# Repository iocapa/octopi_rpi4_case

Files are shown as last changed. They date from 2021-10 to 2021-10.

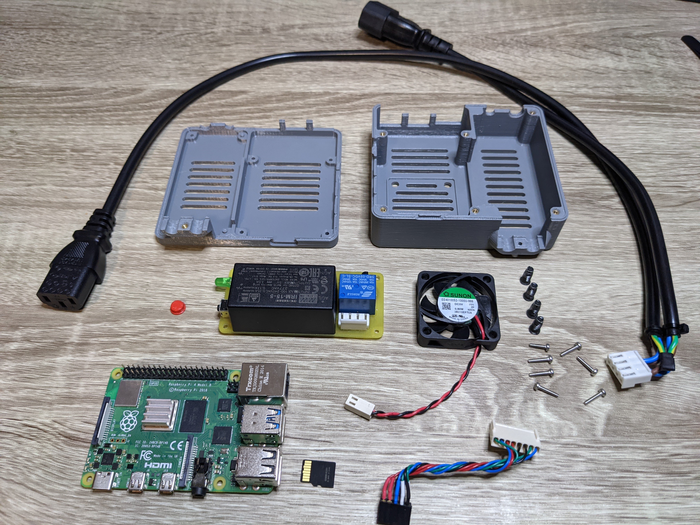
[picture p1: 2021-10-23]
pics/7-parts.jpg

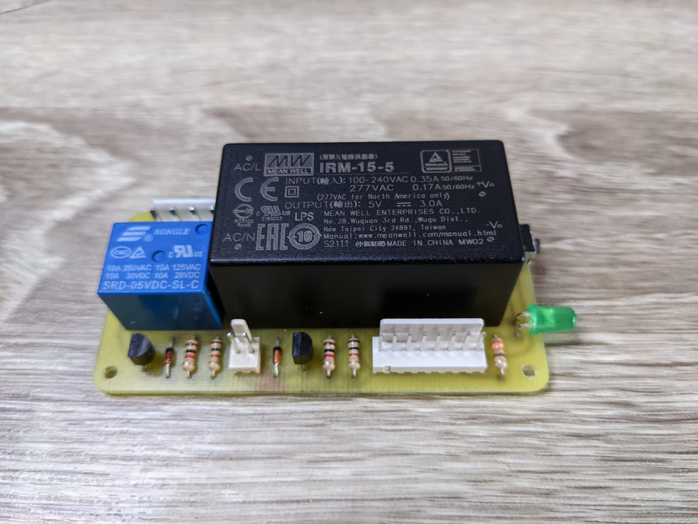
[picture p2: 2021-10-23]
pics/5-assemble.jpg

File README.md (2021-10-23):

Shield: [][cc-by-sa]

This work is licensed under a
[Creative Commons Attribution-ShareAlike 4.0 International License][cc-by-sa].

[][cc-by-sa]

[cc-by-sa]: http://creativecommons.org/licenses/by-sa/4.0/
[cc-by-sa-image]: https://licensebuttons.net/l/by-sa/4.0/88x31.png
[cc-by-sa-shield]: https://img.shields.io/badge/License-CC%20BY--SA%204.0-lightgrey.svg

## Disclaimer ##
Working with mains voltage can be dangerous. Proceed at your own risk.

## Scope ##
* The scope of this project was to create a case for a raspberry pi4 that runs octopi and provides a way to turn off/on the printer (Prusa MK3S+) via the web interface. 
* The project was designed and built during a weekend, therefore it had to be built with parts/tools I had lying around, and it had to be pretty low effort.
* In retrospective, some design decisions were not the "best", but after running this for a week, I'm pretty satisfied with it :).

## Requirements ##
* Shall use a raspberry pi4.
* Shall be compact enough to fit the available space.
* Shall incorporate a relay controllable through the octoprint interface.
* Shall have a status LED.
* Shall have a safe shutdown / power-on button.
* Shall provide active cooling (fan).
* Shall be installable with minimal effort (no mods to the printer).

## Design (Day 1) ##
* ~~Design the [PCB](./pcb/octopi_rpi4_case.pro)~~.
* ~~Design the case [assembly](./assembly/assembly.pdf)~~.

## Build (Day 2) ##
* Print the [top](./pics/11-top.jpg) part of the case and install the brass inserts.
* Cut and [drill](./pics/1-drill.jpg) the blank PCB using the provided [stencil](./pcb/printable/hole_guide.stl).
* [Mask](./pics/2-mask.jpg) the PCB (with a quality permanent marker) using the [template](./pcb/octopi_rpi4_case_bot_mirrored.pdf).
* [Etch](./pics/3-etch.jpg) the PCB.
* [Tin](./pics/4-tin.jpg) the PCB.
* [Populate](./pics/5-assemble.jpg) the PCB using the [template](./pcb/octopi_rpi4_case_silk.pdf) and the [schematic](./pcb/octopi_rpi4_case.pdf).
* [Coat](./pics/6-coat.jpg) the PCB with a thick plastic layer using the provided [mask](./pcb/printable/coating_mask.stl). <span style="color:red">WARNING SKIP THIS AT YOUR OWN RISK</span>, [ECS Plastic 70](https://www.ecsag.com/product/plastic-2/?lang=en) spray works well.
* Print the [bottom](./pics/10-botom-cap.jpg) part of the case and install the brass inserts, print the switch cap.
* Add connectors to the fans and other cables (power and signal) using the [schematic](./pcb/octopi_rpi4_case.pdf) tables.
* [Prepare](./pics/7-parts.jpg) the parts.
* Assemble the [parts](./pics/8-pre.jpg).
* [Assemble](./pics/9-final.jpg) the case using the [video](./assembly/assembly.mp4) and the [instructions](./assembly/assembly.pdf).
* [Install](https://octoprint.org/download/) on your SD card.
* Copy [boot.txt](./software/boot.txt) and [config.txt](./software/config.txt) to the card. Install the card.
* Unplug the printer cord and connect it to the power input and connect the power output to the printer.
* Instal the [OctoRelay](https://plugins.octoprint.org/plugins/octorelay) plugin and configure the printer relay "GPIO Number" to 15.
* Have fun :)

## Special thanks to ##
* [Hasanain Shuja](https://grabcad.com/hasanain.shuja-1) for the RPi4 step model.
* [John Michael Loeffler](https://grabcad.com/john-772) for the Relay and JST connector step models.
* [KiCAD](https://www.kicad.org/), [Raspberry Pi Foundation](https://www.raspberrypi.org/) and [Fusion 360](https://www.autodesk.com/products/fusion-360/overview) for the awesome tools and resources.

## License ##
A [LICENSE](./LICENSE) file is provided with this repository.

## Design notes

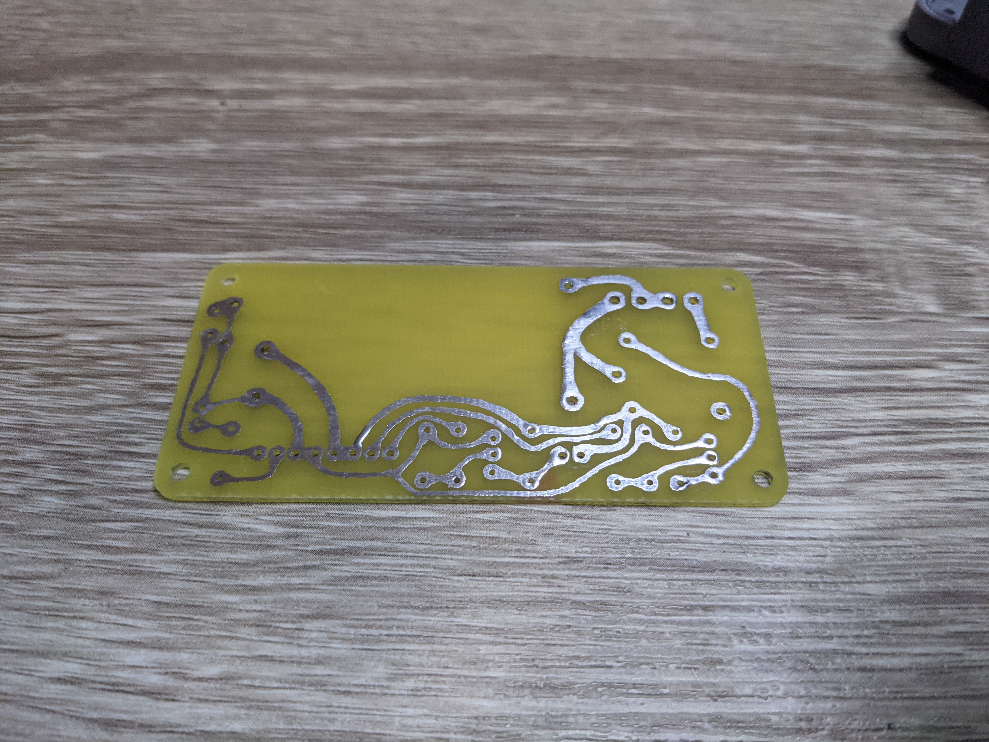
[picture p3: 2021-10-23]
pics/4-tin.jpg

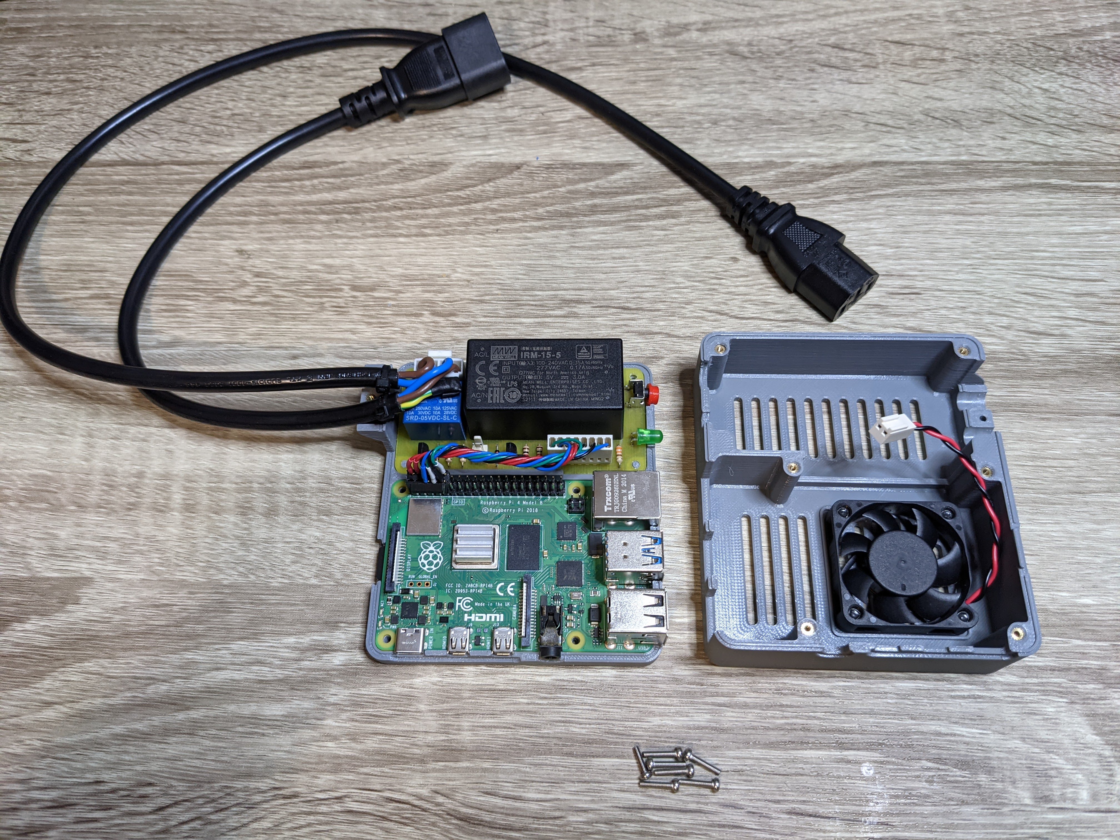
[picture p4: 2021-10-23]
pics/8-pre.jpg

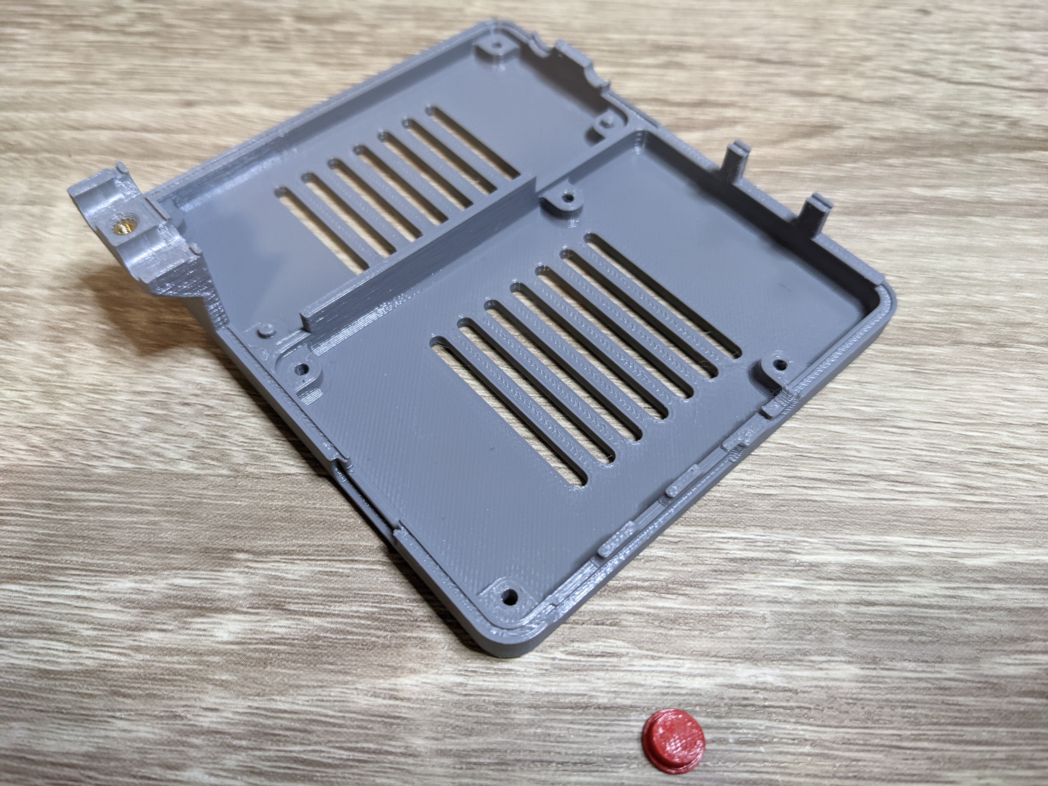
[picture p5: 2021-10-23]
pics/10-botom-cap.jpg

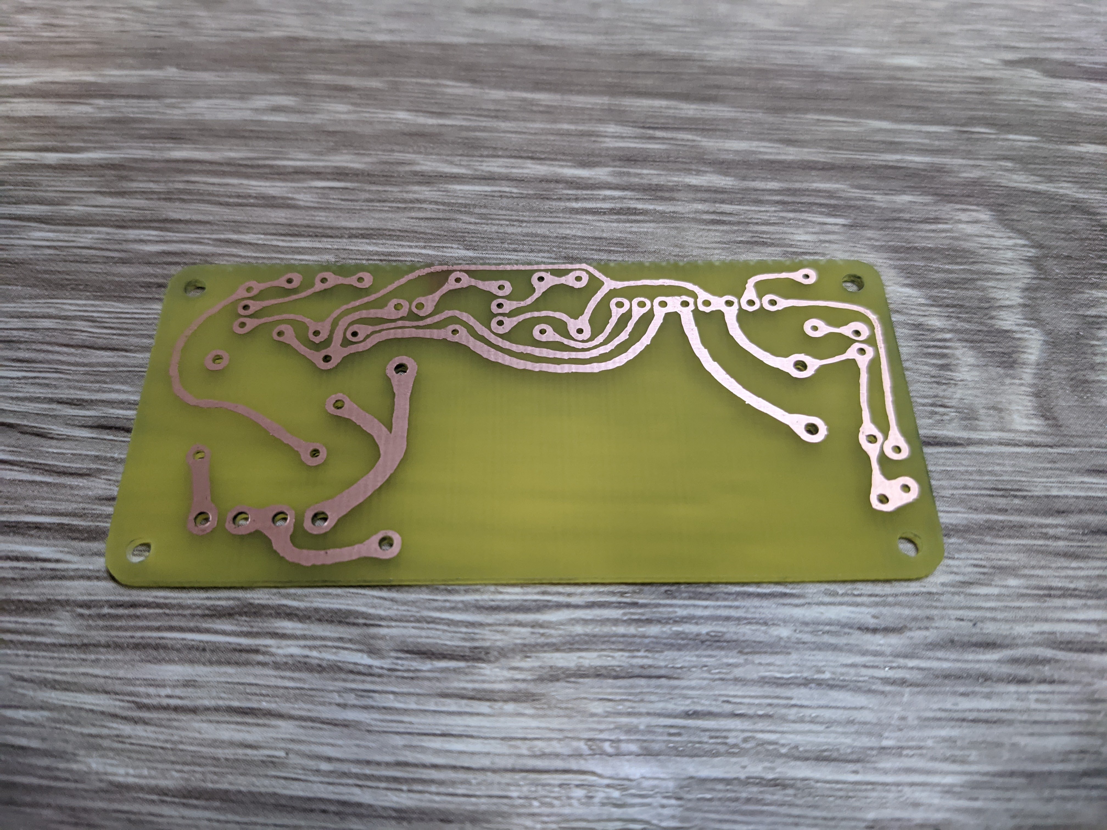
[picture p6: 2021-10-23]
pics/3-etch.jpg

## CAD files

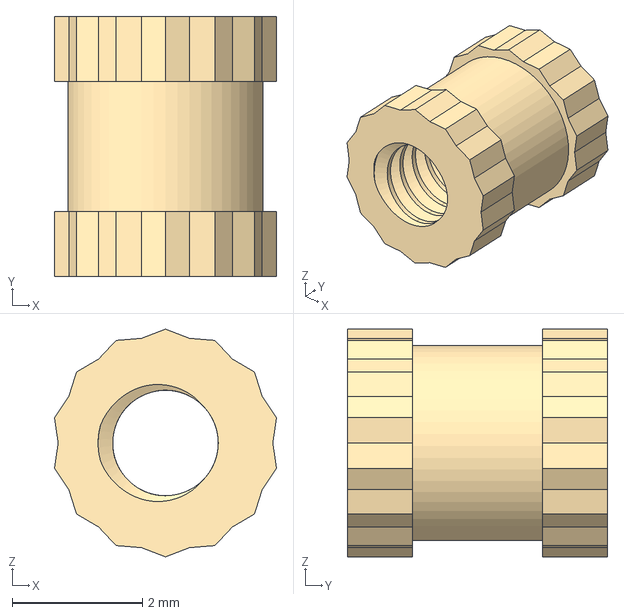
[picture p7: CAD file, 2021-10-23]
assembly/parts/insert_M2x4.step
3.41 x 4.00 x 3.50 mm

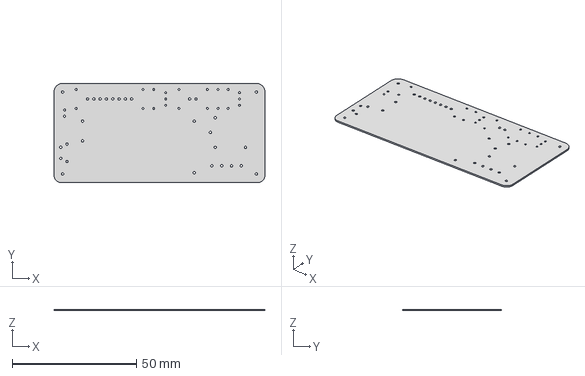
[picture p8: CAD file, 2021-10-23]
pcb/parts/hole_guide.step
85.0 x 40.0 x 0.6 mm

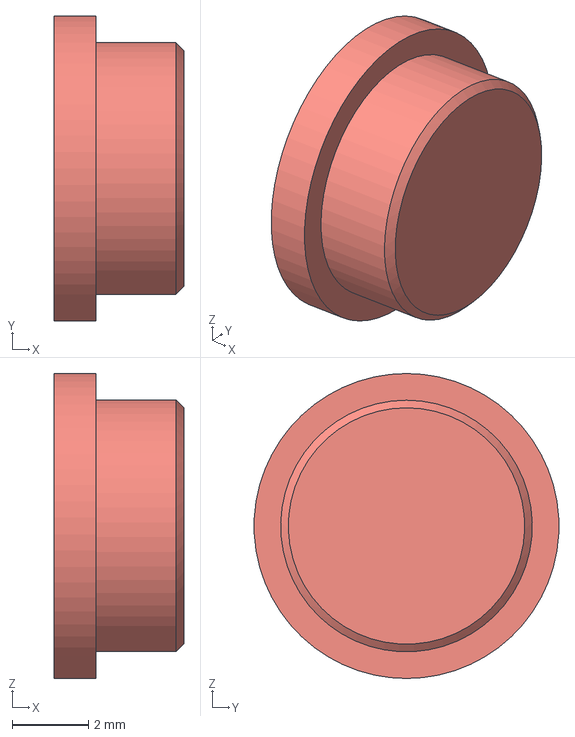
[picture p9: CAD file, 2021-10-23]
assembly/parts/switch_cap.step
3.40 x 7.99 x 8.00 mm

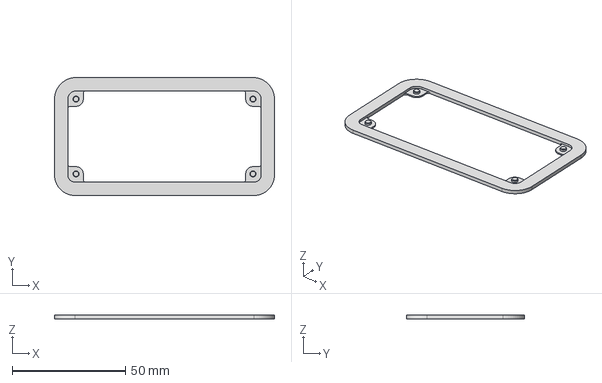
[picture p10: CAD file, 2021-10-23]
pcb/parts/coating_mask.step
97.0 x 52.0 x 1.60 mm

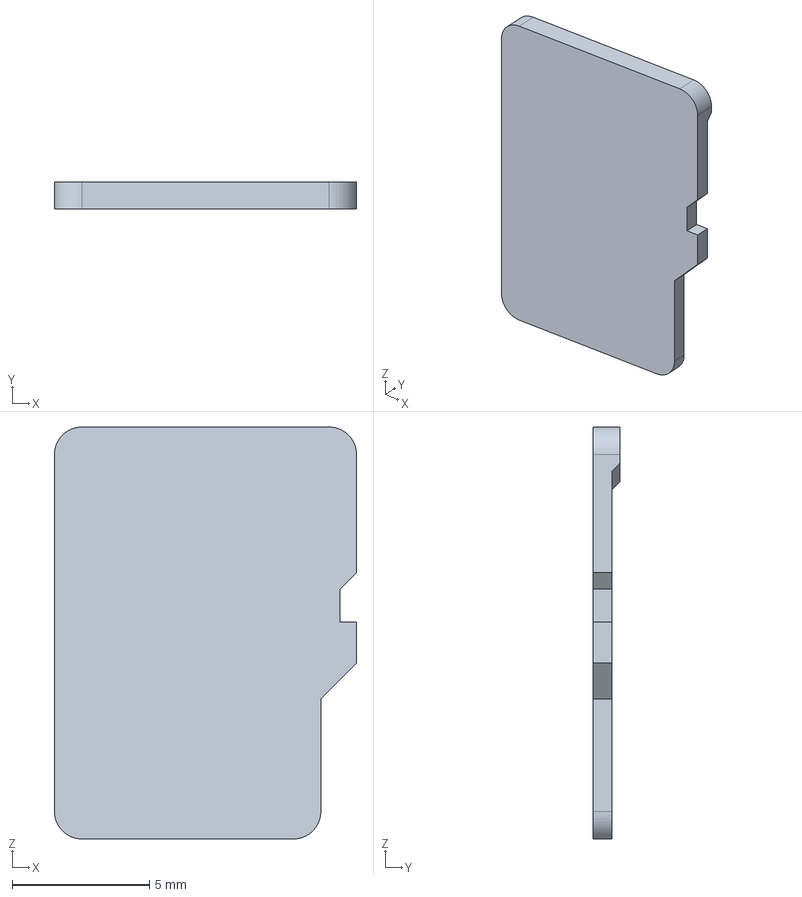
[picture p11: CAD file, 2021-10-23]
assembly/parts/usd_card.step
11.0 x 1.00 x 15.0 mm

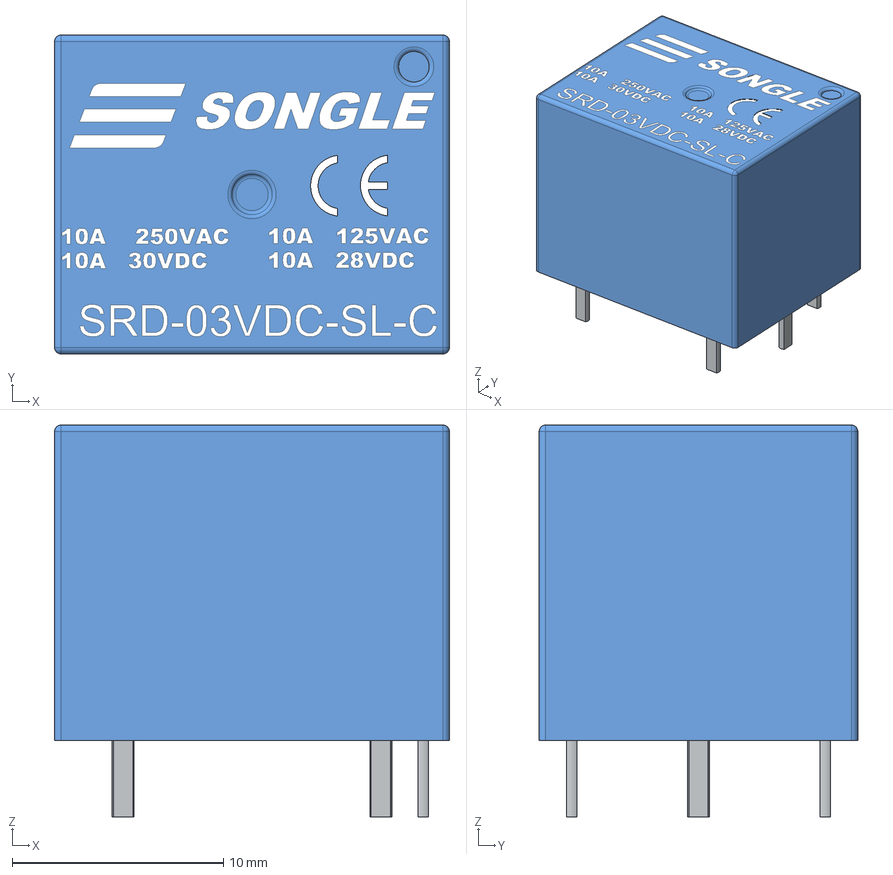
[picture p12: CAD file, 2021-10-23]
pcb/parts/SRD-03VDC-SL-C.stp
18.7 x 15.1 x 18.6 mm

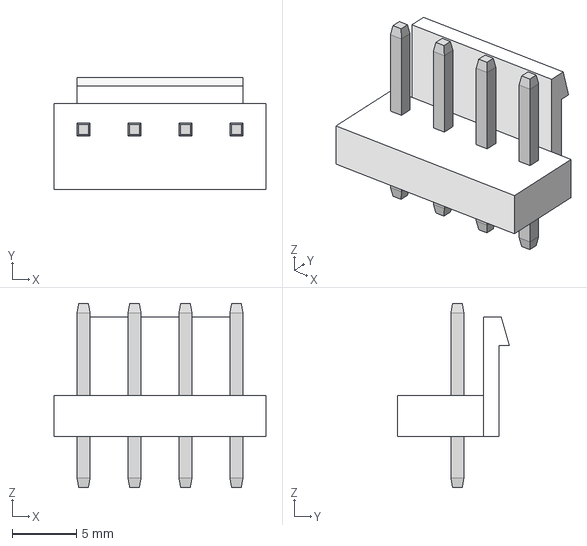
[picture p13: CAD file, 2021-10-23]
pcb/parts/JST - VH - Thru (V) - 4Pin - 3.96mm.stp
16.5 x 8.69 x 14.3 mm

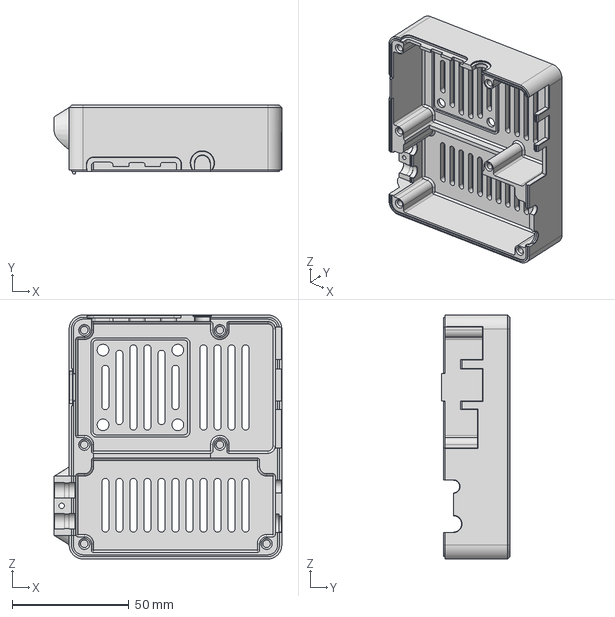
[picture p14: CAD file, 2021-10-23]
assembly/parts/case_top.step
97.4 x 29.4 x 104.4 mm

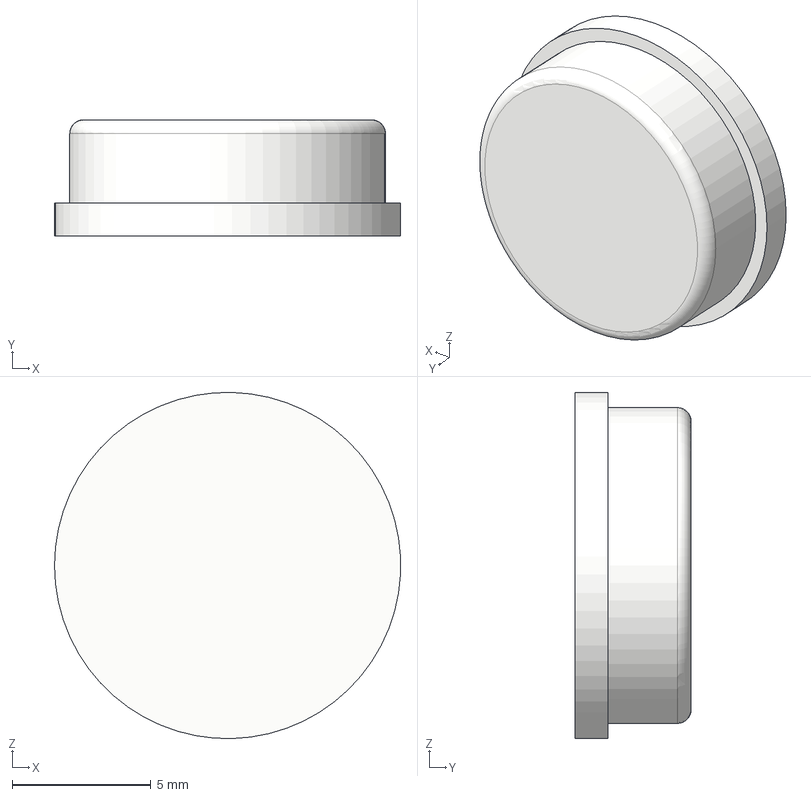
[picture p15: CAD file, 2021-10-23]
assembly/parts/rubber_foot.step
12.5 x 4.20 x 12.5 mm

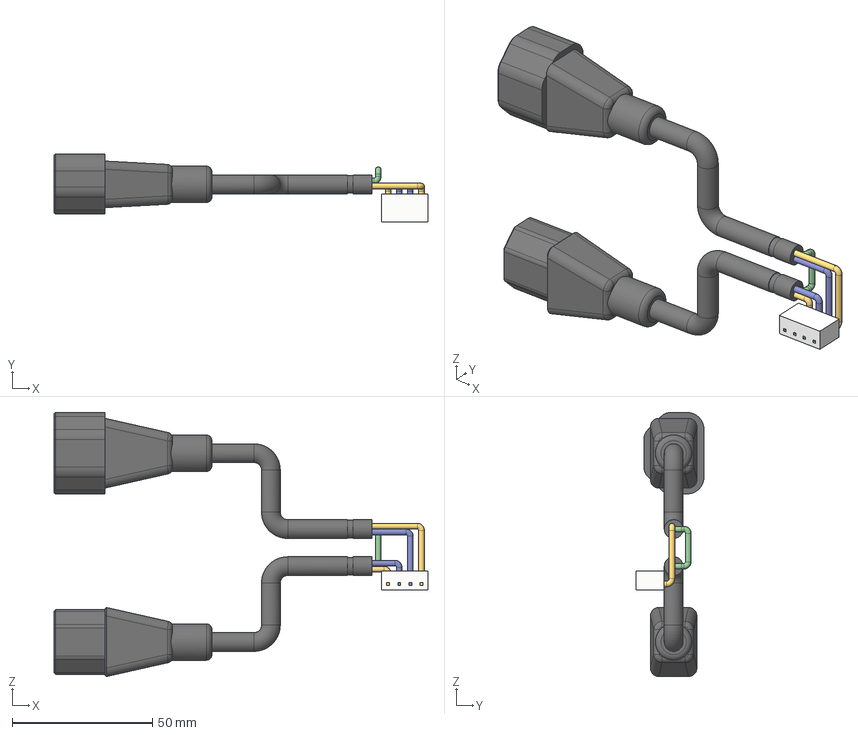
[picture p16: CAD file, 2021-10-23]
assembly/parts/power_wire.step
133.1 x 24.2 x 94.0 mm

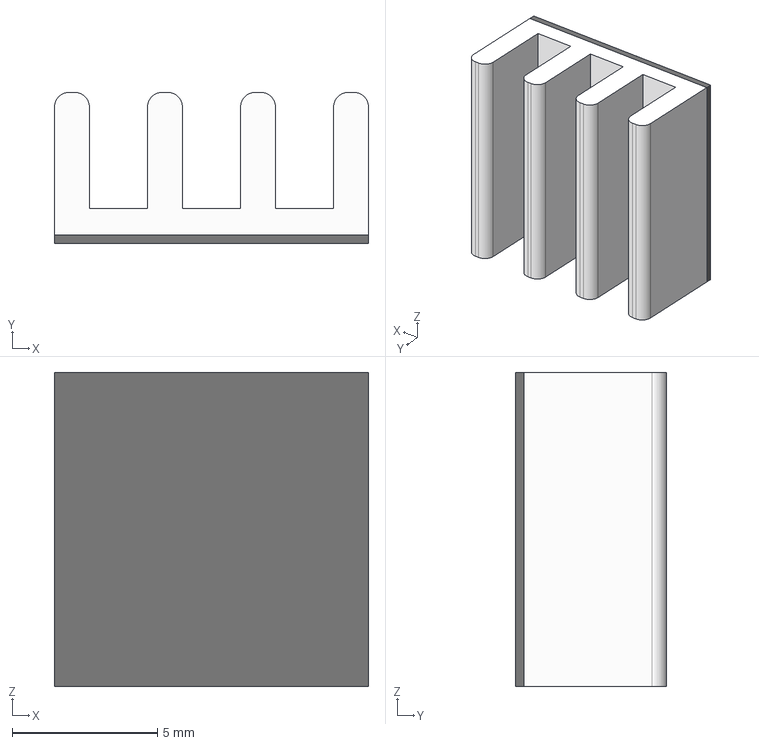
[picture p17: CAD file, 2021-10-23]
assembly/parts/radiator.step
10.8 x 5.20 x 10.8 mm

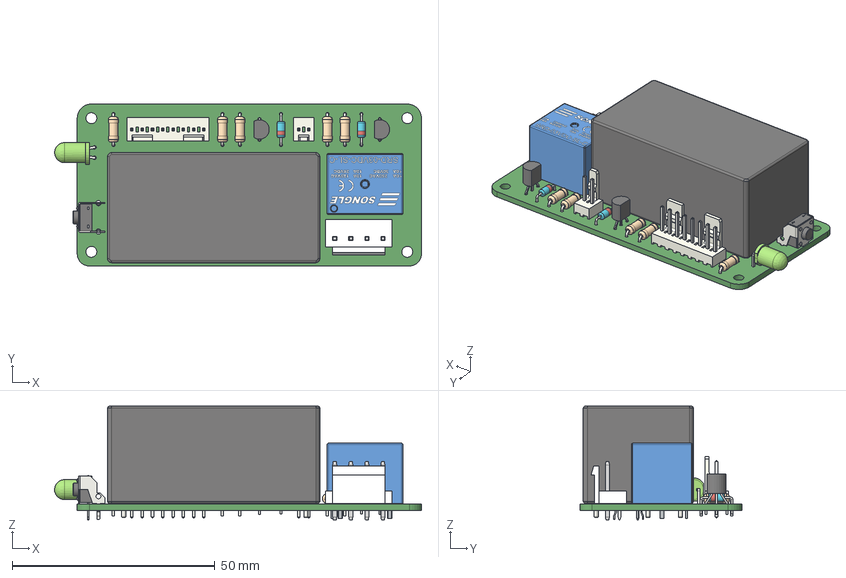
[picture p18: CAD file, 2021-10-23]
assembly/parts/power_module.step
90.6 x 40.0 x 28.1 mm

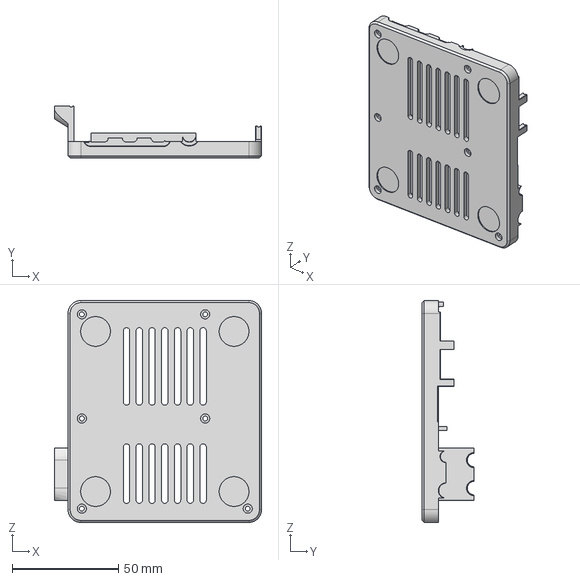
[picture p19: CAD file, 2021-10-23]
assembly/parts/case_bottom.step
97.4 x 24.5 x 104.4 mm

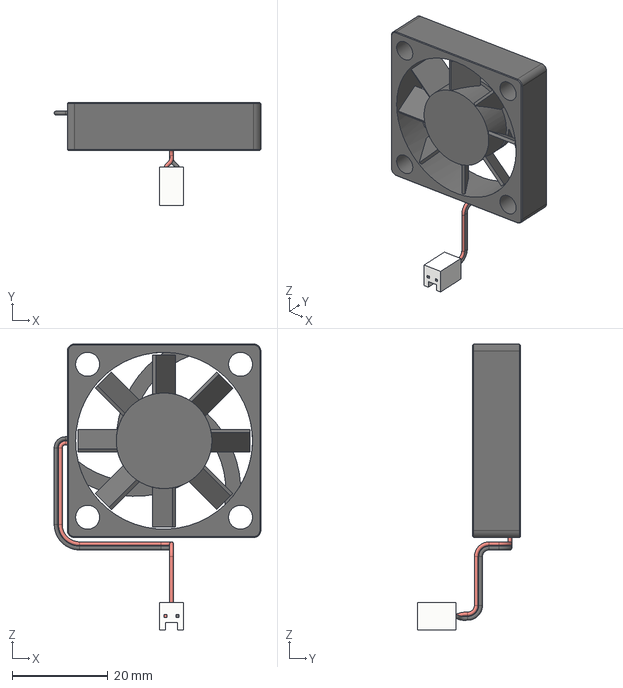
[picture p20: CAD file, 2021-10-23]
assembly/parts/fan.step
43.2 x 21.5 x 59.8 mm

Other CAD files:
assembly/parts/signal_wire.step
assembly/parts/fan_screw_M5x10.step
assembly/parts/allen_screw_M2x9.5.step
assembly/parts/allen_screw_M2x11.5.step
assembly/printable/case_bottom.3mf
assembly/printable/case_bottom.stl
assembly/printable/case_top.3mf
assembly/printable/case_top.stl
assembly/printable/switch_cap.3mf
assembly/printable/switch_cap.stl
pcb/printable/coating_mask.3mf
pcb/printable/coating_mask.stl
pcb/printable/hole_guide.3mf
pcb/printable/hole_guide.stl

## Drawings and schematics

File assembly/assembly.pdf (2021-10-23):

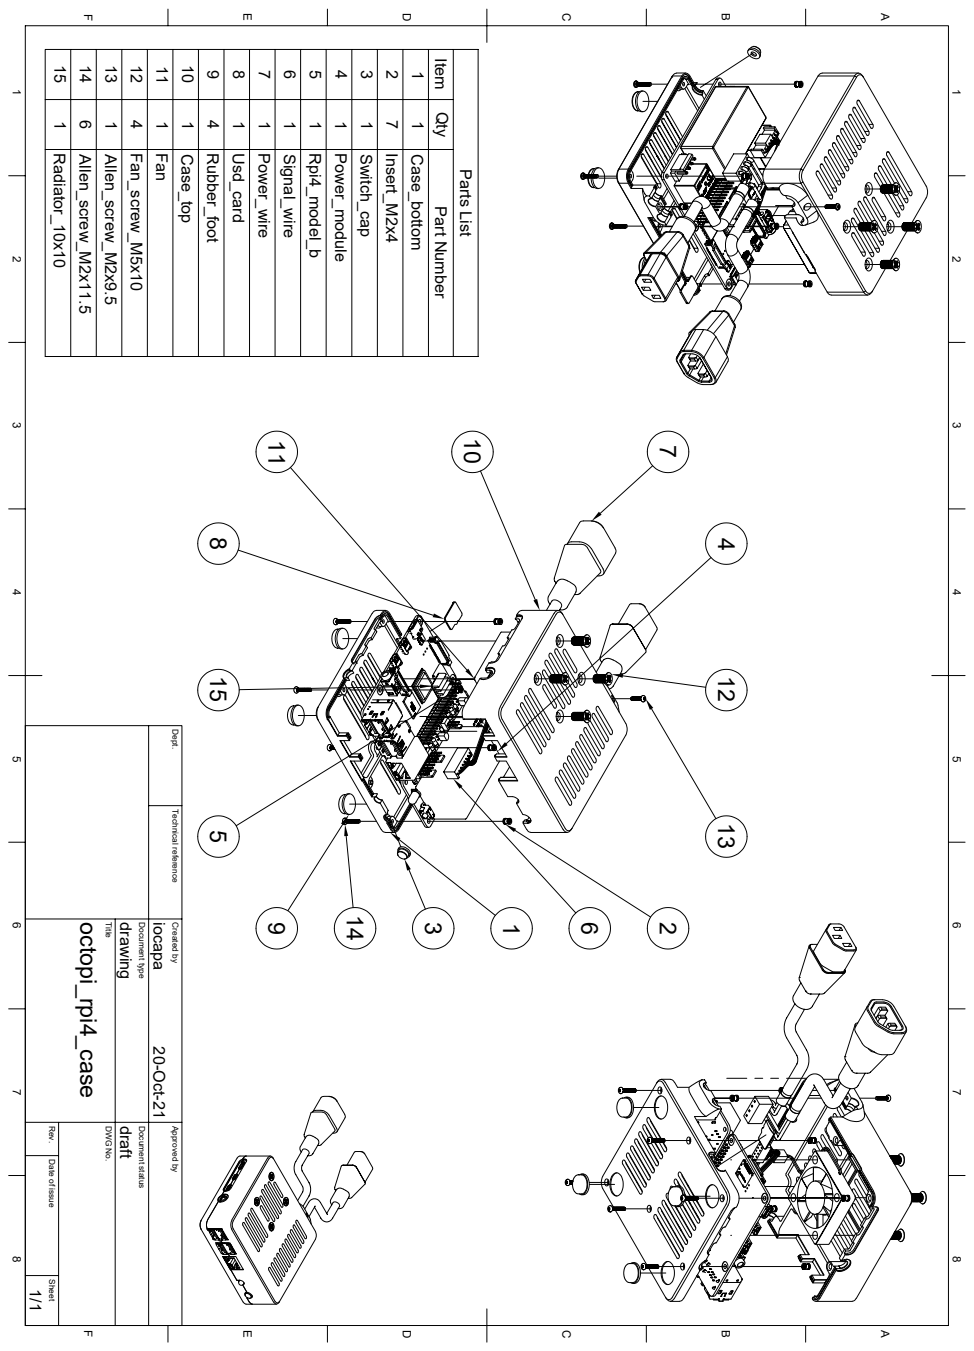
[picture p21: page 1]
Title; Rev.; DWG No.; draft drawing; 20-Oct-21; octopi_rpi4_case; iocapa; Parts List; 1 1 Case_bottom; 2 7 Insert_M2x4; 3 1 Switch_cap; 4 1 Power_module; 5 1 Rpi4_model_b; 6 1 Signal_wire; 7 1 Power_wire; 8 1 Usd_card; 9 4 Rubber_foot; 10 1 Case_top; 11 1 Fan; 12 4 Fan_screw_M5x10; 13 1 Allen_screw_M2x9.5; 14 6 Allen_screw_M2x11.5; 15 1 Radiator_10x10

Item Qty Part Number

Dept. Technical reference Created by Approved by

Document type Document status

Date of issue Sheet

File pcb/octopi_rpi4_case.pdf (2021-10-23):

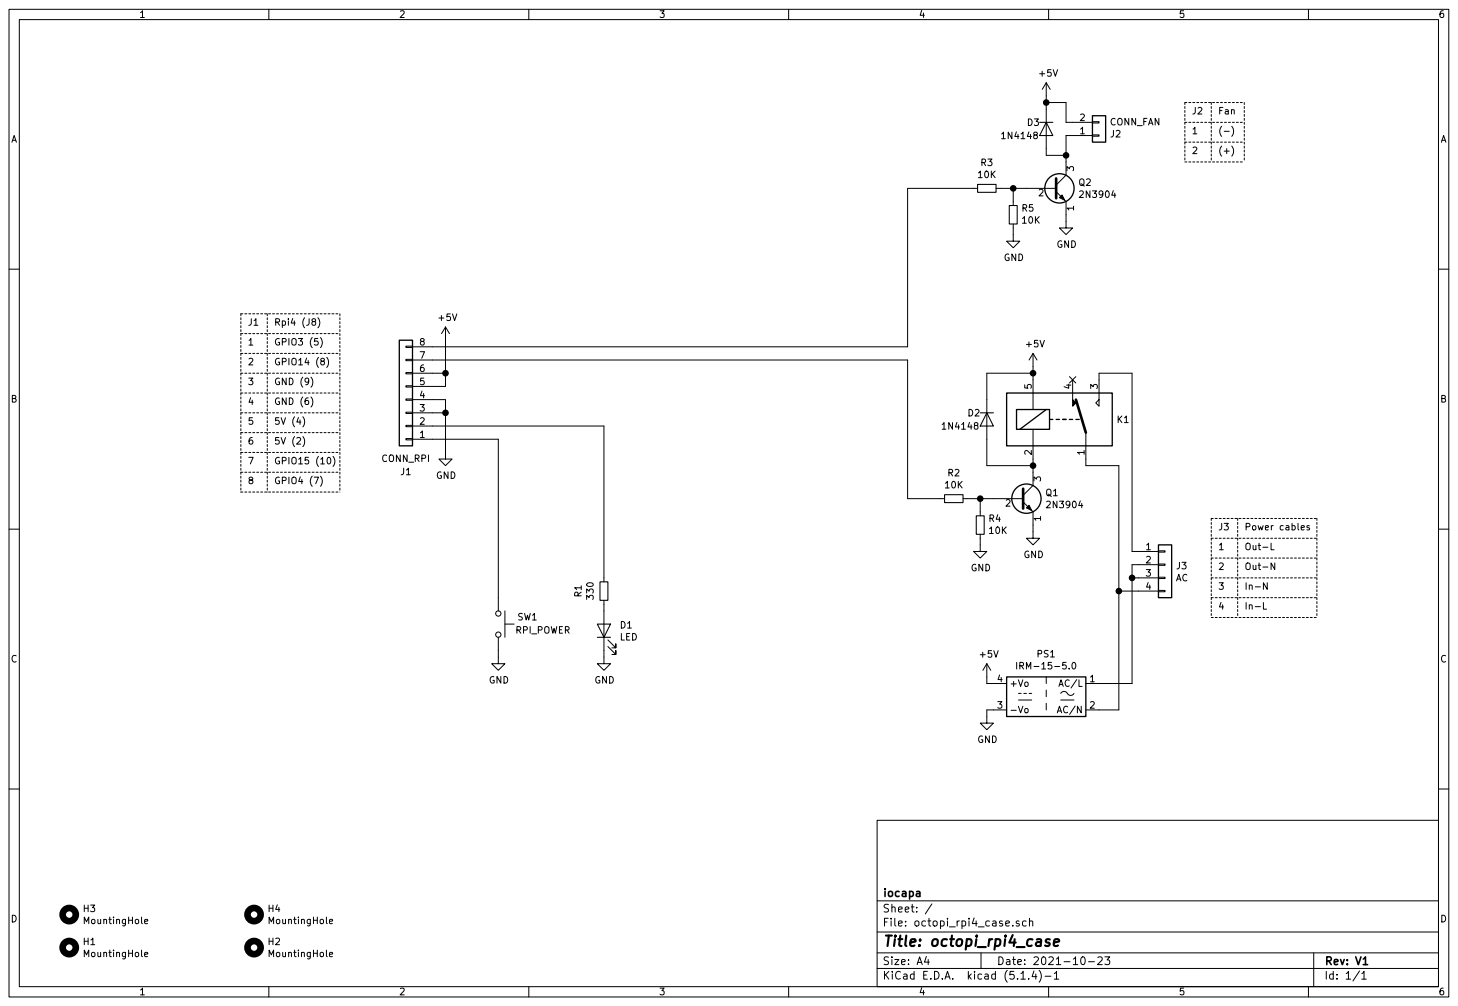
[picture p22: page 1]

2 | 5V (2) 8 Rpi4 (J8) 1
GPIO3 (5)

J3
3 | In-N
In-L

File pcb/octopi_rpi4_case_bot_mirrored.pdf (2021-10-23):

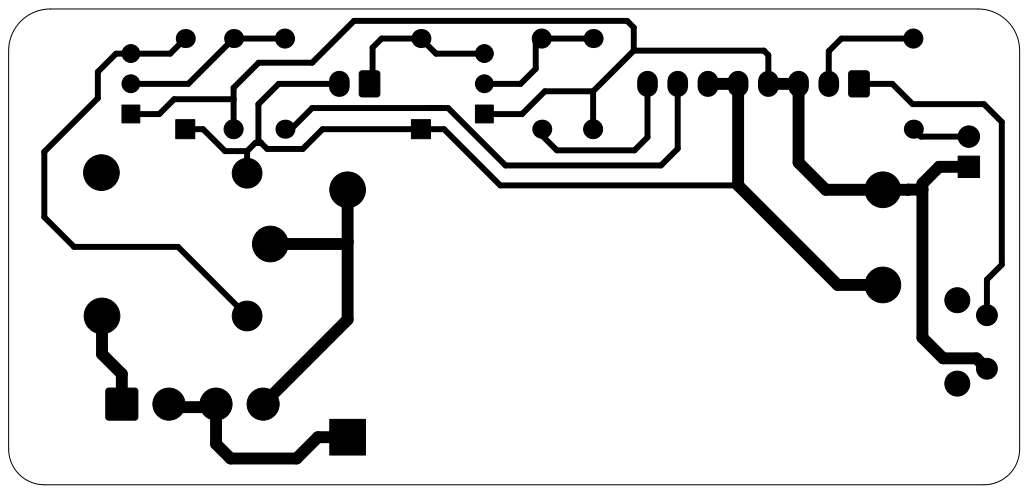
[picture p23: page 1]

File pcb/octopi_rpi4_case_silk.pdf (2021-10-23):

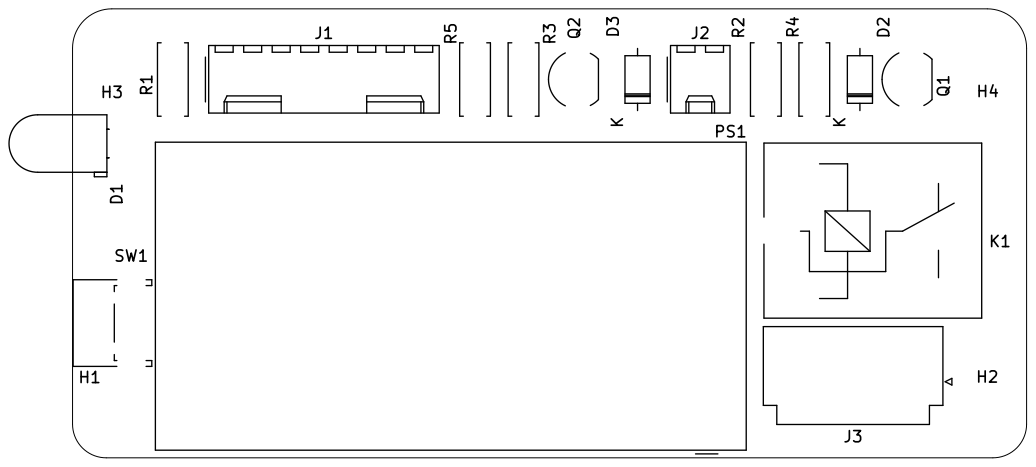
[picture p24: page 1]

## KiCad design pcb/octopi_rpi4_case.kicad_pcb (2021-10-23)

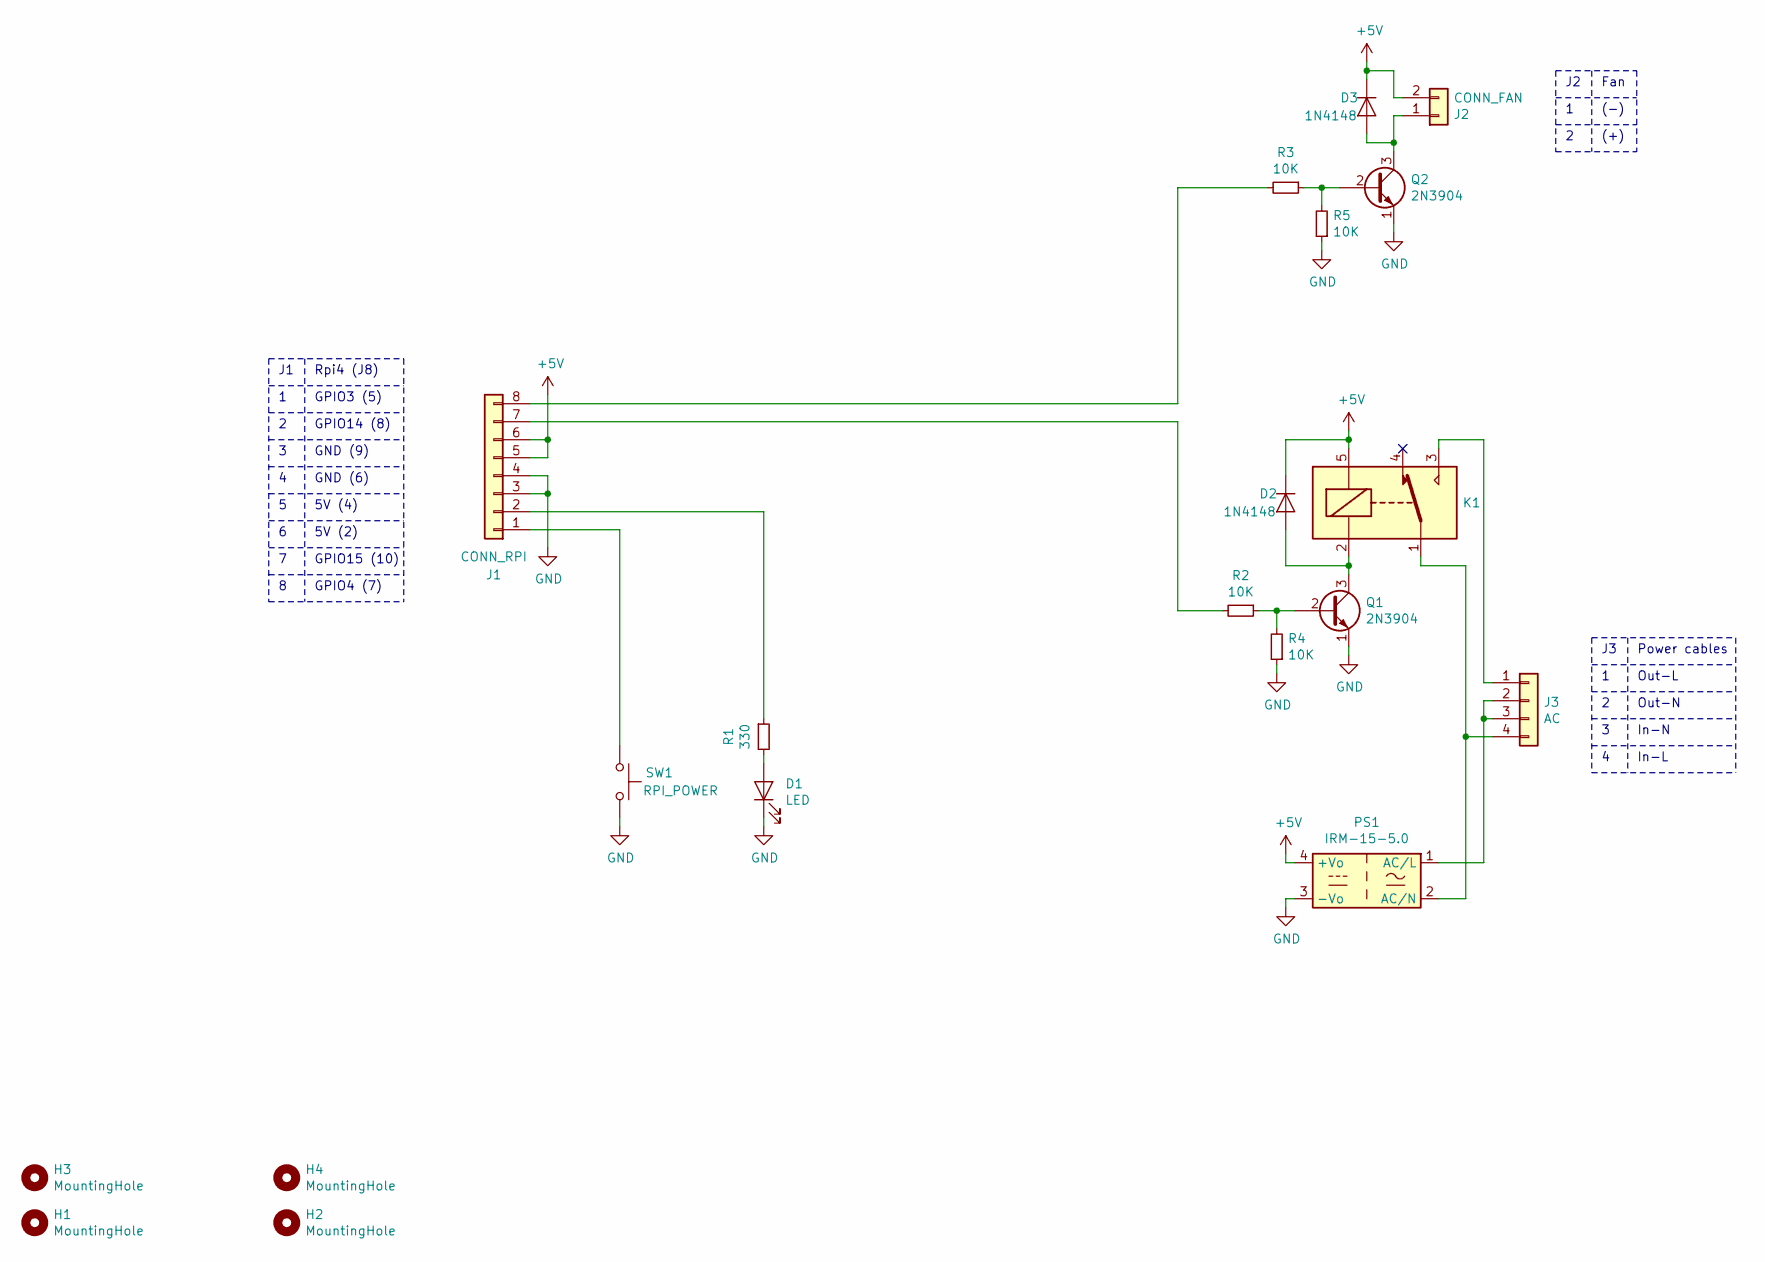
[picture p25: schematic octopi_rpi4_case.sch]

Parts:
D1: LED; LED_D5.0mm_Horizontal_O1.27mm_Z3.5mm
D2, D3: 1N4148; D_DO-35_SOD27_P7.62mm_Horizontal
H1, H2, H3, H4: MountingHole; MountingHole_2.7mm
J1: CONN_RPI; Molex_KK-254_AE-6410-08A_1x08_P2.54mm_Vertical
J2: CONN_FAN; Molex_KK-254_AE-6410-02A_1x02_P2.54mm_Vertical
J3: AC; JST_VH_B4P-VH_1x04_P3.96mm_Vertical
K1: SONGLE-SRD-xxVDC-SL-C; Relay_SPDT_SRD-xxVDC-SL-C
PS1: IRM-15-5.0; Converter_ACDC_MeanWell_IRM-15-xx_THT
Q1, Q2: 2N3904; TO-92_Inline_Wide
R1: 330; R_Axial_DIN0207_L6.3mm_D2.5mm_P7.62mm_Horizontal
R2, R3, R4, R5: 10K; R_Axial_DIN0207_L6.3mm_D2.5mm_P7.62mm_Horizontal
SW1: RPI_POWER; SW_Tactile_SPST_Angled_PTS645Vx39-2LFS

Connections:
+5V: D2.1 (K), D3.1 (K), J1.5, J1.6, J2.2, K1.5, PS1.4 (+Vo)
GND: D1.1 (K), J1.3, J1.4, PS1.3 (-Vo), Q1.1 (E), Q2.1 (E), R4.1, R5.1, SW1.1
unnamed: D1.2 (A), R1.2
unnamed: D2.2 (A), K1.2, Q1.3 (C)
unnamed: D3.2 (A), J2.1, Q2.3 (C)
unnamed: J1.1, SW1.2
unnamed: J1.2, R1.1
unnamed: J1.7, R2.2
unnamed: J1.8, R3.2
unnamed: J3.1, K1.3
unnamed: J3.2, J3.3, PS1.1 (AC/L)
unnamed: J3.4, K1.1, PS1.2 (AC/N)
unnamed: Q1.2 (B), R2.1, R4.2
unnamed: Q2.2 (B), R3.1, R5.2

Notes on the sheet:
Power cables
Out-L
Out-N
In-N
In-L
Fan
(-)
(+)
Rpi4 (J8)
5V (2)
5V (4)
GND (6)
GND (9)
GPIO4 (7)
GPIO15 (10)
GPIO3 (5)
GPIO14 (8)

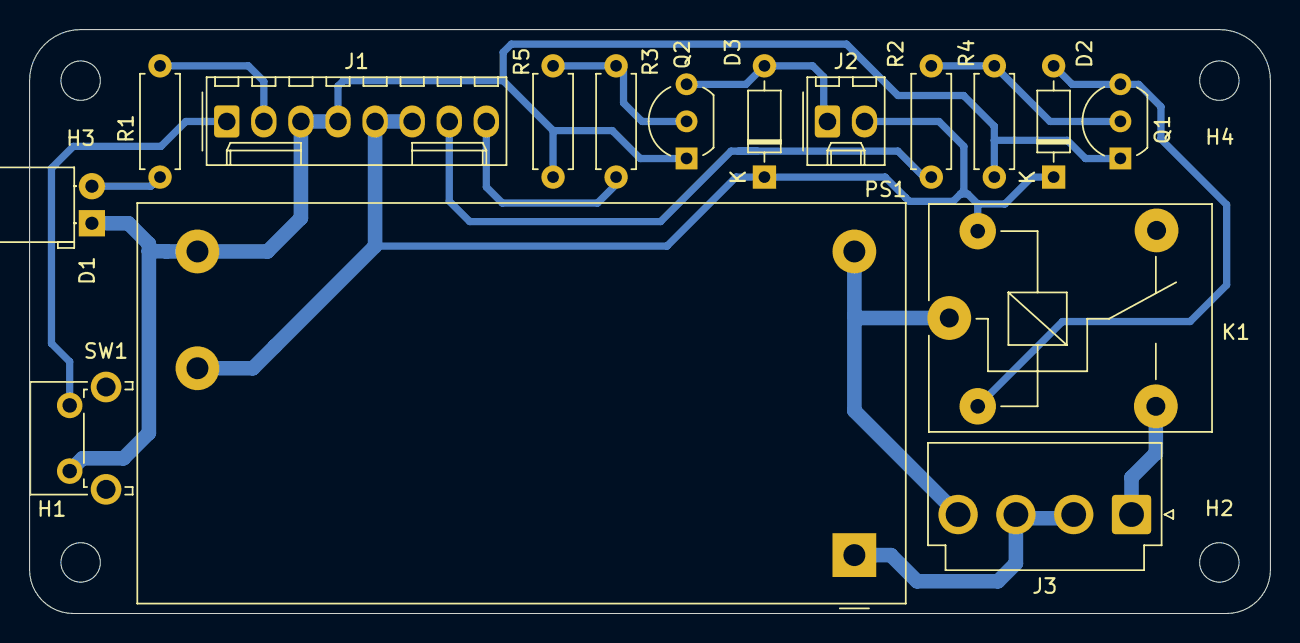
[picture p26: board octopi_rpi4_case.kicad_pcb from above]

Board: 2 copper layers, 85.0 x 40.0 mm, 20 parts (0 on the bottom side), 14 nets.

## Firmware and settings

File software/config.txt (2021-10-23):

# For more options and information see
# http://rpf.io/configtxt
# Some settings may impact device functionality. See link above for details

# uncomment if you get no picture on HDMI for a default "safe" mode
#hdmi_safe=1

# uncomment this if your display has a black border of unused pixels visible
# and your display can output without overscan
#disable_overscan=1

# uncomment the following to adjust overscan. Use positive numbers if console
# goes off screen, and negative if there is too much border
#overscan_left=16
#overscan_right=16
#overscan_top=16
#overscan_bottom=16

# uncomment to force a console size. By default it will be display's size minus
# overscan.
#framebuffer_width=1280
#framebuffer_height=720

# uncomment if hdmi display is not detected and composite is being output
#hdmi_force_hotplug=1

# uncomment to force a specific HDMI mode (this will force VGA)
#hdmi_group=1
#hdmi_mode=1

# uncomment to force a HDMI mode rather than DVI. This can make audio work in
# DMT (computer monitor) modes
#hdmi_drive=2

# uncomment to increase signal to HDMI, if you have interference, blanking, or
# no display
#config_hdmi_boost=4

# uncomment for composite PAL
#sdtv_mode=2

#uncomment to overclock the arm. 700 MHz is the default.
#arm_freq=800

# Uncomment some or all of these to enable the optional hardware interfaces
dtparam=i2c_arm=off
#dtparam=i2s=on
dtparam=spi=off

# Uncomment this to enable infrared communication.
#dtoverlay=gpio-ir,gpio_pin=17
#dtoverlay=gpio-ir-tx,gpio_pin=18

# Additional overlays and parameters are documented /boot/overlays/README

# Enable audio (loads snd_bcm2835)
dtparam=audio=on

[pi4]
# Enable DRM VC4 V3D driver on top of the dispmanx display stack
dtoverlay=vc4-fkms-v3d
max_framebuffers=2

[all]
#dtoverlay=vc4-fkms-v3d
# enable raspicam
start_x=1
gpu_mem=128
[all]

# Fan control (60 degrees)
dtoverlay=gpio-fan,gpiopin=4,temp=60000

# Stutdown button
dtoverlay=gpio-shutdown,gpio_pin=3,active_low=1,gpio_pull=up

# Activity LED pulse
dtparam=act_led_gpio=14
dtparam=act_led_trigger=heartbeat

# Disable power LED
dtparam=pwr_led_trigger=none
dtparam=pwr_led_activelow=off

enable_uart=0

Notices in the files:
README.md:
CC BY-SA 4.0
